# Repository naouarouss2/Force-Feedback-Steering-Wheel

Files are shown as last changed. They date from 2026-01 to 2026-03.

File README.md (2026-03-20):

# DIY FFB Steering Wheel
## What is it ? 🎮
A Force Feedback Wheelbase is a device used in car, truck, bus, or any other 3+ wheeled vehicle (as motorcycles require something different).

The difference between it and a standard game controller is, as the name suggests : **Force Feedback**

Force Feedback is what will create a physical connection between you and the game/simulator you're playing. It will allow you to feel every bump, road imperfection, steering stiffness, vibration... as if you're driving in real life.

## Features ✅
-  **Direct drive**, making it very silent, providing the most accurate and lossless feedback
-  **12-15Nm Force Feedback** (**5.7-7.1x** more powerful than the Logitech G29)
-  **12 Programmable buttons** (Depends on the wheel attached)
-  **Auto center**
-  **0.01125° sensitivity**, making it comparable to some high-end wheelbases on the market

## Why do I want to build it ? 🛠️
I have always wanted to have a simracing setup. Whenever I go to a mall or a gaming café and see a simracing setup, I run like a kid to try it.

I once tried a professional direct drive setup with a motion setup, and this really made me more excited about simracing.

The problem is that the only decent wheelbase available in Tunisia is the Logitech G29 family. They are pretty nice, but overpriced in Tunisia, and it really didn't really fill my heart and satisfy my requirements.

So I wanted to build my own wheelbase, tweaked to my likings and preferences, with endless upgrading and tuning options.

## 3D Design 🎨
I designed everything inside Solidworks, as I am pretty familiar with it, and I already have the CSWA certification.
I divided the design in 2 parts :
-  First, the wheelbase sub-assembly :

| **Full design** | **Aluminium machined parts** | **3D Printed parts** | **Commercial parts** |
|---|---|---|---|
||||

-  Next, the steering wheel sub-assembly

| **Full design** | **Aluminium machined parts** | **3D Printed parts** | **Commercial parts** |
|---|---|---|---|
|||||

And here are pictures of the finished product !


## Wheelbase PCB ⚡
To minimize wiring and make things simpler and cleaner inside, I made a PCB for the wheelbase

| **3D View** | **PCB Routing View** | **Schematics** | 
|---|---|---|
||||

## Wiring Diagrams 🔌
### Wheelbase wiring diagram
fb58e3fb-e4d4-41d1-b4ad-96e4c3caae32
### Steering wheel wiring diagram (made on KiCad, but no PCB)


## Wheelbase Firmware 💡
For the wheelbase, I will be using [OpenFFBoard](https://github.com/Ultrawipf/OpenFFBoard)

## Disclaimer ⚠️

**This project is still under development.**

**Some parts and dimensions in the design should be fixed when I get my hands on the actual componens.**

**Firmware is still untested.**

**This wheelbase can output very high amounts of torque, that may cause injuries.**

**Building is not recommended until everything is made safe ans stable, and the project is completed.**

**If you want to build this project before completion, I would recommend switching from aluminium paddle shifters to 3D Printed ones using the same STEP files, and starting with low force feedback power until the system feels familiar and reassuring, or better, until I finish the development and make sure that the project is safe to use.**

## License 🔓

This project is put opensource. 

Building as is, is allowed.

Remixing is also allowed, as long as the original project is linked and credited.

## Credits ❤️

Project made by **Oussama NAOUAR**

Total logged working time : **~68hrs**

Made as part of the **HackClub Blueprint** program, asking for a grant.

## BOM 💵

This table format below is slightly different from what I originally made in Google Sheets. To to understand it better, I would recommend checking out [BOM.pdf](BOM.pdf)

All prices and shippings costs below are shown in **USD**. For local Tunisian shops, prices and costs were **converted from TND to USD**, based on the exchange rates between **17-12-2025** and **16-12-2025**.

Prices shown below are **non-discounted** prices. These may vary, especially on Aliexpress and other non-local shops.

Shipping costs shown below are **indicative**, based on what Aliexpress and other non-local shops/manufacturers displayed. **These costs may change**.

Articles shown as (x2) are originally only sold as single items, not a 2pcs bundle, with a x2 quantity. And that is done to show the most accurate pricing and shipping fee.

|Type |Component name |Product description |Shop / Manufacturer |Local|URL |Unit price|Shipping|Product Amount|Product Total (excluding shipping)|Product Total (with shipping)|
|---|---|---|---|-----|---|---|---|---|---|---|
|Commercial parts |20*20mm Aluminium Profile|Used to make the wheelbase frame |Seli |Yes  |https://seli.tn/product/20x20-profile-aluminium-industriel-dk/ |15,6 |0 |1 |15,6 |15,6 |
| |40*20mm Aluminium Profile|Used to make the wheelbase frame |Seli |Yes  |https://seli.tn/product/20x40-profile-aluminium-industriel-r6/ |22,5 |0 |1 |22,5 |22,5 |
| |SK16 Brackets |Used to mount the motor in place |Seli |Yes  |https://seli.tn/product/sk16-support-d-arbre-en-aluminium-diam-16/ |3,11 |0 |2 |6,22 |6,22 |
| |UFL004 Bearings |Used to guide the shaft in rotation |Aliexpress |No |https://ar.aliexpress.com/item/1005007098430647.html |17,9 |0 |1 |17,9 |17,9 |
| |ODESC 52V Driver |Used to drive the motor and process FFB Logic |Aliexpress |No |https://ar.aliexpress.com/item/1005005763345874.html |78 |13,2 |1 |78 |91,2 |
| |STM32H743VIT6 Board |Used to control the ODESC board along with the game inputs |Aliexpress |No |https://ar.aliexpress.com/item/1005009563874211.html |11,55 |4,05 |1 |11,55 |15,6 |
| |2000PPR Rotary Encoder |Used to determine the steering wheel's position |Aliexpress |No |https://ar.aliexpress.com/item/1005004387342695.html |15,35 |7,82 |1 |15,35 |23,17 |
| |30-tooth 30mm pulley |Used to tie the encoder's shaft to the steering wheel shaft |Aliexpress |No |https://ar.aliexpress.com/item/1005008678109995.html |4,67 |0 |1 |4,67 |4,67 |
| |Quick release mechanism  |Used to mount the steering wheel to the wheelbase |Aliexpress |No |https://ar.aliexpress.com/item/1005009121231549.html |62,86 |0 |1 |62,86 |62,86 |
| |GX12 Connector kit (M/F) |Used to connect input peripherals to the wheelbase |Tunisian Smart Innovation|Yes  |https://tuni-smart-innovation.com/products/connecteur-male-et-femelle-gx12-4-broches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 |1,49 |0 |5 |7,45 |7,45 |
| |120mm Fan |Used to cool the wheelbase's electronics |2BTrading |Yes  |https://2btrading.tn/ventilateur-radiateur/2391-ventilateur-dc12v-034a-12x12x38cm.html |10,73 | |1 |10,73 |10,73 |
| |XT60M connector |Used to power the wheelbase |Cothings |Yes  |https://cothings.net/products/connecteur-amass-xt60e-m-male |1,73 |0 |1 |1,73 |1,73 |
| |Endstop switch |Game inputs |Cothings |Yes  |https://cothings.net/products/copie-de-capteur-de-temperature-thermistance-ntc-100k-ntc-mf52at-1 |0,45 |0 |2 |0,9 |0,9 |
| |Pushbutton |Game inputs |Cothings |Yes  |https://cothings.net/products/mini-bouton-poussoir-rond-a-reinitialisation-automatique-bleu-etanche-pbs-33b-12mm-2-broches |0,86 |0 |8 |6,88 |6,88 |
| |Hall effect sensor |Used to calibrate the wheel's initial position |Cothings |Yes  |https://cothings.net/products/ky-024-capteur-a-effet-hall-analogique-pour-vitesse-et-comptage |1,55 |0 |1 |1,55 |1,55 |
| |36V 500W Power supply |Used to power the wheelbase |Aliexpress |No |https://ar.aliexpress.com/item/1005003923590693.html |50,53 |10,49 |1 |50,53 |61,02 |
| |GT2-6 400mm belt |Used to connect the shaft pulley to the encoder pulley |2BTrading |Yes  |Courroie GT2-6 400mm |3 |0 |1 |3 |3 |
| |Seed XIAO RP2040 |Microcontroller for the steering wheel |Aliexpress |No |https://ar.aliexpress.com/item/1005003682505451.html |4,78 |4,52 |1 |4,78 |9,3 |
| |Steering Wheel |The actual steering wheel |Aliexpress |No |https://ar.aliexpress.com/item/1005009791304312.html |25,99 |42,53 |1 |25,99 |68,52 |
| |TJA1051 |CAN transceiver |Aliexpress |No |https://ar.aliexpress.com/item/1005005569468051.html |4,1 |0 |1 |4,1 |4,1 |
| |12V Buck Converter |Used to power the fan |Aliexpress |No |https://ar.aliexpress.com/item/1005008597548688.html |2,6 |7,28 |1 |2,6 |12,48 |
| |5V Buck Converter |Used to power the MCU and other peripherals |Aliexpress |No |https://ar.aliexpress.com/item/1005008597548688.html |2,6 | |1 |2,6 | |
| |USB-C Female Connector |Used to connect the wheelbase to the computer |Aliexpress |No |https://ar.aliexpress.com/item/1005009695057393.html |11,62 |0 |1 |11,62 |11,62 |
| |USB-C 90° cable |Used to transfer the USB connection from the PCB to the external connector|Aliexpress |No |https://ar.aliexpress.com/item/1005002708307702.html |6,4 |4,79 |1 |6,4 |11,19 |
| |USB-C Breakout Board | |Aliexpress |No |https://ar.aliexpress.com/item/1005004807492800.html |4,19 |0 |1 |4,19 |4,19 |
| |JST-XH 4 Pin Connector |Used to make cable connections easier |Tunisian Smart Innovation|Yes  |https://tuni-smart-innovation.com/products/connecteur-jst-xh2-54-4-broches-male-femelle-avec-cable-de-20-cm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 |0,7 |0 |5 |3.5 |3.5 |
| |JST-XH 3 Pin Connector |Used to make cable connections easier |Tunisian Smart Innovation|Yes  |https://tuni-smart-innovation.com/products/connecteur-jst-xh2-54-3-broches-male-femelle-avec-cable-de-20-cm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|0,62 |0 |1 |0,62 |0,62 |
| |JST-XH 2 Pin Connector |Used to make cable connections easier |Tunisian Smart Innovation|Yes  |https://tuni-smart-innovation.com/products/connecteur-jst-xh-2-broches-male-femelle-avec-cable-de-20-cm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 |0,49 |0 |1 |0,49 |0,49 |
| |M2X10 Screw |Screw diameter = 2mm, length = 10mm |Already have | |N/A |0 |0 |4 |0 |0 |
| |M3x10 Screw |Screw diameter = 3mm, length = 10mm |Already have | |N/A |0 |0 |8 |0 |0 |
| |M3x16 Screw |Screw diameter = 3mm, length = 16mm |Already have | |N/A |0 |0 |10 |0 |0 |
| |M4x8 Screw |Screw diameter = 4mm, length = 8mm |Already have | |N/A |0 |0 |8 |0 |0 |
| |M4x16 Screw |Screw diameter = 4mm, length = 16mm |Already have | |N/A |0 |0 |4 |0 |0 |
| |M5x16 Screw |Screw diameter = 5mm, length = 16mm |Already have | |N/A |0 |0 |6 |0 |0 |
| |M5x36 Screw |Screw diameter = 5mm, length = 36mm |Already have | |N/A |0 |0 |4 |0 |0 |
| |M5x50 Screw |Screw diameter = 5mm, length = 50mm |Already have | |N/A |0 |0 |6 |0 |0 |
| |M6x20 Screw |Screw diameter = 6mm, length = 20mm |Already have | |N/A |0 |0 |4 |0 |0 |
| |M10x16 Screw |Screw diameter = 10mm, length = 16mm |Already have | |N/A |0 |0 |2 |0 |0 |
| |M3 Nut |Nut diameter = 3mm |Already have | |N/A |0 |0 |4 |0 |0 |
| |M10 Nut |Nut diameter = 10mm |Already have | |N/A |0 |0 |2 |0 |0 |
| |M3 Aluminium Profile Nut |Nut for aluminium profiles, diameter = 3mm |Seli |Yes  |https://seli.tn/product/ecrou-marteau/ |0,1 |0 |4 |0,4 |0,4 |
| |M4 Aluminium Profile Nut |Nut for aluminium profiles, diameter = 4mm |Seli |Yes  |https://seli.tn/product/ecrou-marteau/ |0,1 |0 |8 |0,8 |0,8 |
| |M5 Aluminium Profile Nut |Nut for aluminium profiles, diameter = 5mm |Seli |Yes  |https://seli.tn/product/ecrou-marteau/ |0,1 |0 |4 |0,4 |0,4 |
| |M6 Aluminium Profile Nut |Nut for aluminium profiles, diameter = 6mm |Seli |Yes  |https://seli.tn/product/ecrou-marteau/ |0,1 |0 |4 |0,4 |0,4 |
| |Table clamps (x2) |Used to mount the wheelbase on the table |Aliexpress |No |https://ar.aliexpress.com/item/1005006458478718.html |47,8 |8,28 |1 |47,8 |56,08 |
| |Hoverboard motor |Used to provide force feedback |Facebook Marketplace |Yes  |N/A |19 |0 |1 |19 |19 |
| |TOTAL | | | | | | | |453,11 |556,07 |
|PCB |Wheelbase PCB |Holds the various electronic components without the need for wiring |JLC PCB |No |N/A |2 |21,91 |1 |2 |21,91 |
|Aluminium machined parts|Front plate | |JLC CNC |No |N/A |8,72 |49,48 |1 |8,72 |72,77 |
| |Back plate | |JLC CNC |No |N/A |10,63 | |1 |10,63 | |
| |Paddle (x2) | |JLC CNC |No |N/A |3,94 | |1 |3,94 | |
|GRAND TOTAL | | | | | | | | |478,4 |650,75 |

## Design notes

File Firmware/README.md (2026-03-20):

In this folder, you will find the firmware for the ~wheelbase~, as well as the firmware for the steering wheel itself.

**Disclaimer ⚠️ :** None of these firmwares had been tested on hardware.

For the OpenFFBoard configurator tool, you can find it in this [official OpenFFBoard repository](https://github.com/Ultrawipf/OpenFFBoard-configurator/tree/9eee2b5ffe44f2dec1c6d2eae4a0ad987d53b5c8) :

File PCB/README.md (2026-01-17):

Here you will find all of the Wheelbase PCB files.

Extensions  :
-  Project : .kicad_pro
-  Schematic : .kicad_sch
-  PCB : .kicad_pcb
-  Footprint libraries created and used : .pretty
-  Symbol libraries created and used : .kicad_sym

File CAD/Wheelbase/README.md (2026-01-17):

Hexagonal holes in the 3D Printed parts are for magnets (not modeled).
Aluminium profile nuts were not modeled. But every screw that is going in an aluminium profile rail will need a matching nut.

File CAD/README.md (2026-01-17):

Here you will find all of the design ressources for this project.

**Disclaimer ⚠️ :** Some dimensions may not be accurate yet. Some files will be updates as soon as I get my hands on the actual parts to take measurements.

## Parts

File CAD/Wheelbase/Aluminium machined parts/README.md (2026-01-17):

The back plate should have threaded holes for the electronics mounting holes (M3 screw holes).

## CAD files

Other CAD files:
CAD/Full_assembly.STEP
CAD/Steering Wheel/Steering_wheel_sub-assembly.STEP
CAD/Wheelbase/Wheelbase sub-assembly.STEP
CAD/Steering Wheel/3D Printed parts/Paddle Holder.STEP
CAD/Steering Wheel/Aluminium machined parts/Paddle.STEP
CAD/Steering Wheel/Commercial parts/QR Sample.STEP
CAD/Wheelbase/3D Printed parts/Clamp Surface Flattener.STEP
CAD/Wheelbase/Aluminium machined parts/Front plate.STEP
CAD/Wheelbase/Commercial parts/KFL004.STEP
CAD/Steering Wheel/3D Printed parts/Paddle Shifter Mount.STEP
CAD/Wheelbase/3D Printed parts/Hall Eff Sensor Mount.STEP
CAD/Wheelbase/Aluminium machined parts/Back plate.STEP
CAD/Wheelbase/Commercial parts/Side 2040 profile.STEP
CAD/Wheelbase/PCB.step
CAD/Steering Wheel/3D Printed parts/Back Enclosure.STEP
CAD/Wheelbase/3D Printed parts/Top cover.STEP
CAD/Wheelbase/Commercial parts/Clamp Sample.STEP
CAD/Steering Wheel/3D Printed parts/Front.STEP
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

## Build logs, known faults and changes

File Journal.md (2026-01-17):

<!--
  This journal is auto generated by Hack Club Blueprint.
-->

## 12/17/2025 - 3D Design Pt.1  

_Time spent: 2.5h_  

**17-12-2025**
Today, I started working on the 3D Design of the wheelbase.

To get some inspiration, I went on YouTube and watched a lot of different designs of wheelbases that used a hoverboard for FFB.

The simplest design is to use aluminium profiles for the frame and motor mounting. And to hold the steering wheel axis, I decided to go with 5mm cnc-cut aluminium sheets for the front and back plates. And for cool aesthetics, I will design some 3D-printed parts to complete the enclosure.

For today, I started by designing the 30*30mm aluminium profiles that will go on the sides between the front and back plates.


I then went on to design the front and back plates.

And after that, I designed the aluminium profile that would hold the hoverboard mounting brackets.

And finally, I put everything inside an assembly to start seeing what the wheelbase will look like.


Up until now, except for the aluminium profiles' sketches, every dimension is roughly entered, just to get a better idea of what the design will look like. 
As I get further into the 3D design, and get a better overall idea about the project and components' dimensions, I will enter the right dimensions.

## 12/18/2025 6:29 PM - 3D Design Pt.2  

_Time spent: 2.0h_  

**17-12-2025**
After I took a dinner break, I got back to CAD.

I changed the side aluminium profiles to 20*20mm instead of 30*30mm since they're a bit cheaper, and will make it easier to link them together using the L brackets. I also corrected the 20*40mm profile sketch.

After doing some research, I found that the most popular hoverboard motor size is 6.5 inches. So I went on Grabcad and imported a motor model.

After importing the motor, I designed the SK16 mounting bracket that I'll be using to secure the motor to the aluminium profile.

After doing the assembly, I noticed that the motor will sit a bit lower than the enclosure, so I needed to raise it.

I designed a riser to go between the middle profile and the SK16 brackets, but I didn't want to put a plastic part in the motor holding assembly. So I changed the bottom aluminium profiles to some 20*40mm to raise the motor higher, and therefore eliminate the need for a plastic riser.

I also squared up the front and back plates to make it easier to understand the dimensions.



## 12/18/2025 6:49 PM - 3D Design Pt.3  

_Time spent: 1.0h_  

**18-12-2025**
Today, since I had 2hrs of free time at school, I decided to make some adjustments to my current 3D design.

First of all, I lowered the middle profile, the one to hold the motor on, to sit right between the bottom side profiles. This will make for a much sturdier mount with screws on the sides, instead of relying on friction generated by the nuts and L brackets.

But this made it mandatory to have a 3D Printed riser underneath the SK16 brackets.
I did a lot of experimenting to make the spacer as short as possible, but the minimum height I could go with was 23mm.

I also made the entire wheelbase height a bit smaller, to have the motor sticking out a bit on the upper side and have better aesthetics when designing the 3D Printed enclosure.

I also made the wheelbase much shorter, as I decided to make a 3D-printed enclosure to go on the back to house the electronics.

Up until now, my design is very inspired from this design made by "Orhan Kökbudak" on Grabcad :
https://grabcad.com/library/direct-drive-wheelbase-1

Here is my design up until now  : 

Of course the tire will be removed from the motor. It's just that I didn't find a way to do it on that specific STEP file :)

Now the next challenge is to find a way to mount the steering wheel shaft to the motor.

## 12/19/2025 7 PM - 3D Design Pt.4  

_Time spent: 4.0h_  

**18-12-2025**
This time, I did some adjustments to what I did last time, and modeled 2 new components.

First of all, I had to find a way to mount the shaft onto the hoverboard motor.

I asked my mechanics teacher and he proposed to make a mount on a lathe using a thick tube (I forgot the material's name). 

This part will then have 6 holes to mount it on the motor, and a hole to mount the shaft using a bushing. But the thickest diameter he had was only 50mm, and that is really thin, as we have to make the mounting holes as far appart as we can, to avoid drilling into the bearing inside the motor.

At first, I didn't want to use a 3D Printed part for the most critical component of this project. But then, I decided to make a thick part that will be printed in PETG with 100% Infill, and it should work just fine. I saw people doing the same thing, and they didn't have any problems.

So I hopped on Solidworks and drilled some holes on the motor model, and then designed the shaft mount.
At first, I put some approximate shaft dimensions since I didn't decide the shaft diameter.
I tried making it with the biggest fillet possible to make it as sturdy as it can be.

Then I went on the internet, and chose 16mm as shaft diameter, and asjusted the mount accordingly.


Then, I decided to use a traditional rotary encoder, unlike most people on the internet who used magnetic encoders, since it will reduce complication and eliminate the need to drill through the motor.

The encoder will be linked to the shaft using a belt and pulley setup.

I didn't find any good models online of the encoder, so I designed one myself following a datasheet on Aliexpress.


I then proceeded to make the encoder mount. 
It took me a lot of prototyping. At first I made a model that should be mounted on the top side of the bottom aluminium profiles. But that would make the encoder really close to the shaft.

I didn't decide the pulleys that I'll be using so I wanted to space them apart, and make space for a belt tensioner.

So I made a mount that will stick from the side of the profile.


And finally, I went back on the internet to choose the pulleys. Since it was already very late at night, I left their 3D design for the next time.

Here's what I achieved up to this time. 



## 12/19/2025 10 PM - 3D Design Pt.5  

_Time spent: 3.3h_  

**19-12-2025**
Today, I made a very important step-up in the 3D Design.

**1. Encoder Pulleys**

Yesterday, I chose some pulleys with an 8mm bore diameter. I thought that I'll make a part of the shaft thinner using the lathe, but I didn't think about how I'm gonna slide the shaft pulley in its slot. So I had to look for pulleys with a much bigger bore, and unfortunately, these aren't available in Tunisia. 

At first, I thought about building a pulley in the shaft mount which will be 3D Printed, but I didn't wanna rely on 3D Printing for precision. The whole point of the pulley setup is better resolution; 3D printing might ruin that.

After a lot of research, and trying to understand pulley names, I fould on Aliexpress a pulley with 20mm bore diameter. So I made a sample3D pulley in Solidworks to see how it will be mounted. I also switched to a 20mm shaft, which will be sturdier.
I also made a sample pulley design for the encoder.

Since the shaft pulley turned out to be bigger than expected, I made the wheelbase larger to make space for a pulley tensioner. I also slightly modified the encoder mount to sit slightly higher

**2. External Design**

I completely redesigned the front and back plates.

They are larger now, and feature a nice and dynamic design in my opinion.
I also adjusted the mounting holes positions to make space for the 3D-printed enclosure.
The top aluminium profiles are now mounted at an angle.



## 12/20/2025 8 PM - 3D Design Pt. 6 ; A major redesign !  

_Time spent: 1.5h_  

**20-12-2025**
Last time, I tried to replicate Moza's wheelbase design. But I went by mind, no visual reference, so I got it very wrong !
This time, I took a closer look at Moza's wheelbase design and got onto redesigning the entire face plate.
I also found a new way to mount the encoder without the need to use a belt tensioner, so this enabled me to make the wheelbase less wide. I didn't design the new encoder mount yet, but I started by removing the old one and narrowing the wheelbase.


## 12/20/2025 10 PM - CAD Pt.7 ; Failed pulley system redesign attempt  

_Time spent: 2.0h_  

**20-12-2025**
As I said in my previous journal, I found a better way to mount the encoder, that will eliminate the need for a belt tensioner. I got inspired by this design on YouTube :
https://youtu.be/X-Dd3wjQ4uM?si=eNiLrp9AvPEiq4_C

Basically, the encoder is mounted on the back side of the motor, on the same rails as the motor mounting shafts. And this will allow the encoder to slide left and right to get the right amount of belt tension.
But this required a very big pulley that will be mounted on the back side of the motor rotor, and it had to be custom built.

I first made the new encoder mount that will also be 3D printed just like the older one.

Then I added it to the assembly, and everything was looking pretty nice at this point.


Now came the big motor pulley design. And I first thought that I would find ressources and standard dimensions like most normalized parts out there. But I really couldn't find any.
I tried copying the design mentioned earlier, but I couldn't get the STEP file to something that I can reliably get measurements from.
I tried following this YouTube Tutorial, https://youtu.be/6EBqo_BrOmA?si=bFQslmDhV668M_lL but the teeth came out really big, and I couldn't fit 120 teeth in a diameter smaller than the motor's.

So as of now, I think that I will keep the old design, make the wheelbase larger, and design a belt tensioner later.

## 12/21/2025 - CAD Pt.8 ; Success in making the pulley  

_Time spent: 1.2h_  

**20-12-2025**
The great thing about me is that I don't give up easily.
So after dinner, I kept looking for ways to make the pulley, and I found this tutorial uploaded by Solidworks :
https://youtu.be/rjmKaswKXUc?si=Y-1p3jga44CPzpXg
So I followed it and made my custom 120-tooth pulley that will be mounted on the back of the motor.

Next, I made a sample 30-tooth pulley to be mounted on the encoder to have a 4:1 ratio to have 4x the encoder resolution.

Next, I mounted everything in the assembly, and here's what it looks like now :


## 12/22/2025 1 AM - Cad Pt.9  

_Time spent: 3.0h_  

**21-12-2025**
**1. Front Bearing**
To finish with the front plate, I searched for 20mm bearings and found a model called UFL004.
This bearing has a way to mount it with screws to the front plate, thus without needing to make custom brackets...
So I designed a sample model without details, just the important dimensions

Then, I made holes accordingly in the front plate to house this bearing.
https://youtu.be/vjENDQarwxI?si=C9ZFouVhPo-rN4WJ
**2. Back Plate**
Nothing special here. Saved a copy of the front plate, removed the bearing holes, and added it to the assembly.

**3. The enclosure**
Since I'm now pretty confident that the front and back plate designs won't change, I made the external enclosure.

This enclosure will be printed in 4 separate parts : Left, Right, Upper, Lower enclosure, so I designed each part on its own to fit flush with the plates and aluminium profiles.

I also kept the bottom aluminium rails exposed since they will be used for the desk mount.

Since the front plate's sketch is very complicated, I tried looking for a way to make the part inside the assembly to make it easier. So this time, I sketched the enclosure parts directly inside of the assembly, thanks to this tutorial :
 
It is the first time that I make a part within the assembly in Solidworks. And this will certainly help me a lot in this project and in the future project.



## 12/22/2025 11 PM - CAD Pt.10 ; Electronics Enclosure  

_Time spent: 3.0h_  

**22-12-2025**
This time, I made the enclosure for the electronics, that will be mounted at the back, behind the Aluminium back plate.

I used that amazing feature that allows you to design a part within the assembly, and it made my life a lot easier again :)

I first started by designing a very simple enclosure.

Then, I started thinking about the ports that I'll be using for future pedals, shifter, button box... connections.

At first, I thought about making a PCB with RJ45 ports, but then said that making a PCB just to add 4 connectors is really a loss.

So I started searching for available connectors at my local shops and stumbled upon these amazing GX12 connectors.


They directly mount onto the enclosure, so no need for a PCB, screws, whatsoever. I'll just need to solder wires, that's all.

I also decided to add a 120mm fan on the back to cool down the motor driver, and the motor too; that's why I chose a big fan.

And finally, I also decided to put an XT60 connector on the back to power everything on, as the power supply will be separate, so that the wheelbase doesn't get bulkier.



## 12/23/2025 - CAD Pt.10 ; Some vents + components placement  

_Time spent: 2.0h_  

**23-12-2025**
I started by adding some vents on the sides, on both the front and back side panels.



Then, since I chose from the beginning, by watching similar setups online, to use ODESC as a control board for FFB, I downloaded this model from Grabcad to place it in the assembly and start making holes to mount each component. (By the way I'll go through the electronics soon, I just need to finish CAD first).

https://grabcad.com/library/odesc-v4-2-bldc-motor-driver-controller-1

The guy did a really good job at making a very detailed model. But unfortunately, my computer only has 8GB of ram, and an iGPU. So here is where the struggle begins :)

Immediately after adding the component to the assmebly to verify dimensions etc... everything started going very very slow on my computer. So from now on, everything I did later was really slow, including some modifications to the back panel to make mounting holes, and making the back enclosure a bit shorter.

But eventually, I placed it along with the included resistor. And I placed them on the far right to make them close to the power supply connector, and to take benefit of a maximum airflow coming from the vents to the fan.
Here is how it is mounted : 


## 12/24/2025 2 AM - CAD Pt.11 ; Steering Wheel Hub  

_Time spent: 3.5h_  

**23-12-2025**
Today, I decided to take a break from the wheelbase design, and start working on the wheel itself.
For a first wheel, I decided to make things pretty simple and reliable.

I decided to use a Momo steering wheel or similar, like the ones used in drift cars. I still didn't choose the model, but they all have the same 6-screw mounting system.
The wheel will also feature a quick release system. 

I spent a lot of time on Aliexpress looking for a reliable and easy to mount quick release system. 
A lot of them tricked me since they showed cheap prices at first, but they were all "Welcome deals".
The cheapest decent one that I found is this one.
https://ar.aliexpress.com/item/1005009121231549.html
And bonus : Someone already used it for a simracing setup in the reviews !

With that in mind, I went to design a shaft mount for this quick release module. 


Next, I went on to design the hub that will be stuck to the steering wheel. This hub will contain all of the buttons, paddle shifters... and all of the wiring.
First, I designed the back plate that will be mounted to the QR mechanism.

There are 12 holes : 6 for the QR mechanism, and 6 to mount the front plate and the steering wheel.

Here is the front plate, that will house (for now, just as an alpha prototype version) 8 buttons.

The 2 plates will be spaced by about 3.5cm to make space for the wiring inside + paddle shifters mounted on the sides.
The 2 plates will be spaced by using screw spacers.

And to hide everything, I made this enclosure


Then, I made a small cylinder with approx dimensions as a sample for the quick release mechanism, just to tell that it's there.

And finally, I made everything into a sub-assembly :


## 12/24/2025 7 PM - CAD Pt.12  

_Time spent: 2.5h_  

**24-12-2025**
I know, CAD is taking very long, but we're very close :)

First of all, I modified all of the wheel hub parts so that they become modular and linked to eachother, so that when I edit one of them, I don't get errors, and every part get automatically rebuilt.
I did that by sketching the parts inside of the assembly.

Then, I added two joystick holes to the front plate
.

After that, I got to designing the magnetic paddle shifter assemblies.
I tried to do something very similar to what this guy did :
https://youtu.be/Fp4gQ_euMsg?si=-S9PfVIbnG-W44iQ
I started by making the paddle

Then I slowly made the other parts by myself, keeping in mind that guy's amazing work.
After that, I put everything into a new sub assembly.

Up until now, I thought that everything had been done properly. But that changed quickly when I tried putting the sub-assembly into the wheel hub sub-assembly.



Not only was the assembly designed backwards, meaning that to activate the switch you need to push the paddle, but the mounting holes were also wrongly placed in a way that they would hide behind the quick release mechanism.

It was very frustrating to see 2hrs of work lost. But it happens !

I think that I'll use the parts from the YouTube video, as fixing my model will take a lot of time.
He provided STL parts in the Google Drive linked in the description, as well as DXF files for the laser-cut parts, from which I will tzke dimensions to put on my design for the mounting holes.

## 12/25/2025 - PCB Design Pt.1 ; First steps in KiCad :)  

_Time spent: 4.5h_  

**25-12-2025**
This time, I decided to take a break from the 3D Design !

Remember when I said that a PCB isn't necessary because I only needed to wire 4 connectors ? Well it turned out that I was wrong.

After doing some more research on YouTube and the OpenFFBoard GitHub and Discord server, it turned that it is a bit more than just connectors.

For the electronics, I will be using  the ODESC board as mentioned before. But on top of that, I will be using :

- An STM32H7 board to handle the game inputs
- A 12V regulator to power on the fan
- A 5V regulator to power the STM32 board along with providing power to the GX12 connectors
- A TJA1051 CAN transcoder so that the ODESC and STM32 board can communicate
- A hall effect sensor 

So to keep things tidy and more reliable (as I always tend to make a mess when wiring up a lot of components manually), I decided to make a small PCB.

Before thinking about the wiring diagram, since I knew the components that I'll be using, I first chose my PCB editor : Altium Designer.

Why Altium ? Because it was the only software that had a STM32H7 board library available online.
And this is a very critical decision so that I don't have bad surprises when I make good progress later on.

At first, I thought that it would be pretty easy to get started, but then I found the software to be very complex, and not beginner friendly.

I started looking for alternatives that supported Altium libraries, and I found KiCad, so I downloaded it eventually. And believe me, the light theme and simple-looking interface really comforted my mind and brought me my motivation back.

To test it, I tried by importing the Altium Library. The import process was pretty easy, but I soon ran into issues. 

The board was imported in 2 symbols, and the biggest and most important one isn't working at all. I couldn't place any wire. And when going to PCB editor, it automatically inserted two whole boards instead of one, and none of them was working.

And since I already apreciate the user-friendly interface, I decided to make my own symbol and footprint for the STM32H7 board.

I found this tutorial on YouTube, and slowly but surely, I started getting the hang of it.

https://youtu.be/OzF5vsgkLAY?si=zL08rsIuo40u2LD9
https://youtu.be/NiSkKemLK_8?si=Aa3ntH2me7qxCW7M

I followed the tutorial while following an image of the board online. I chose a generic board since I thought that they were the cheapest, and made the symbol accordingly. But when I checked on Aliexpress, these generic boards were cheap indeed, but shipping to Tunisia was very expensive. So I chose to make the WeAct board instead, since it was cheaper overall. So I saved it and kept it. Maybe I'll need it in the future, who knows !?

And fortunately, the corrupt library had the exact same symbol pin layout as the WeAct one, so it made it easier since I basically had to copy it. Here's what I made :


Next, is the footprint layout !

I downloaded the 3D STEP model from this Github

https://github.com/WeActStudio/MiniSTM32H7xx

And by taking measurements from the model in Solidworks, and following the tutorial above, here is what I came up with :


To connect components to this PCB, I chose to use some JST XH connectors. Essentially 2-pin, 4-pin and 5-pin variants.

I found the footprints in KiCad, but I could not find the symbols. So I made a symbol for each variant and linked it to its matching footprint.



## 12/26/2025 - PCB Design Pt.2 ; The schematics  

_Time spent: 3.5h_  

**26-12-2025**
First, I made the missing components for the pcb, the symbol + footprint.
The missing components were :

- 3P JST XH connector for the Hall Effect Sensor
- TJA1051 CAN Transceiver
- The buck converters (I will use 2 of the same model for both 5V and 12V outputs)

Next, after continuing to watch the tutorial series that I linked yesterday, I started looking for the cheapest PCB manufacturer that makes high quality PCB. And I chose JLC PCB as it was the cheapest of all, and had very good reviews and apparently a good build quality.
Then, by using the link provided in the video's description, I imported all  of the settings and tolerences for JLCPCB machines to KiCad.

After that was done, I started making the schematics for the wheelbase's PCB.
First of all, I placed all of the components in a way that would make it more understandable for me to work on. 

For the JST XH connectors, I used : 

- 4 4-Pin connectors for the GX connectors on the wheelbase to connect the peripherals
- A 5-pin connector for the encoder
- A 3-pin connector for the hall effect sensor
- A 2-pin connector for the ODESC CAN input
- A 2-pin connector to power up the electronics from the main 36V power input
- A 2-pin connector to power up the fan from the 12V buck converter
- A 4-pin connector for the ST-Link programmer

I then renamed all of the components so that they make sense.

Then I connected all of the connectors 1st and 2nd pins to GND and +5V respectively, of the 5V buck converter's output.

Then, I wired up the TJA1051 module to a CAN port of the STM32H7 board by following the official datasheet.

Then I wired up all of the 4-pin connectors to different UART ports of the STM32 board, as these will be used to connect peripherals.

And finally, I connected the encoder to 3 timer pins of the STM32H7 board with a 510-Ohm resistor for each channel. I saw people doing that when using a 5V encoder with an STM32 board on VNM discord server, so I thought that it was to protect the 3.3V pins, so I added the resistors.

Here is how the schematics turned out :


## 12/27/2025 2 AM - CAD Pt. 13 ; Wheel Hub Redesign  

_Time spent: 2.0h_  

**27-12-2025**
Back to CAD again :)
At 12:30AM, I got the very bright decision to completely redesign the steering wheel hub !

I started doing some research regarding CNC cutting aluminium sheets, and it is pretty expensive, and useless to be honest.
So I decided to make the steering wheel hub entirely 3D-Printed. 
And this time, I got inspired by Fanatec's Clubsport Universal Hub design.


So first of all, I started designing the face plate, with, just like Fanatec's hub, 4 triangles to hold 3 push buttons each. I made it triangular so that it fits well with the wheel, and kept a big hole for the quick release mechanism to go through, to the wheel itself.


Then I put it inside of an assembly, along with the buttons and the QR sample model to see how everything looks.

After that, I started designing the enclosure that will go behind that plate, and will house the wiring and paddle shifters, directly inside of the assembly.

Unfortunately, the thick enclusure walls meant that most of the quick release mechanism was going to be inside of that enclosure, and make it impossible to operate the mechanism. So I headed back to the front plate design, and made a built-in spacer that would push the quick release mechanism out of the enclosure, just enough so that it can be operated.



For now, I put an approximate spacer thickness since I don't know how thick the quick assembly mechanism really is, and how thick the enclosure will be. So once I finish the hub design, and get my hands on the mechanism, I would be able to insert the right dimensions.

## 12/27/2025 11 PM - PCB Design Pt.3 ; PCB Routing Complete !  

_Time spent: 4.0h_  

**27-12-2025**
This time, I went to finish with the PCB so that I could finish CAD once and for all.

Last time, I made the schematics, so today, all I had to do was the PCB layout and wiring.

I first placed the components as shown in the image below. I wanted the PCB to be as small as possible, and as easy to route as possible.


As you can see, to minimize routing complication, I put the ST-Link connector just above the SDIO header of the STM32 board, the power connector just besides the buck converters' inputs, the encoder resistors just above the header pins...

And since the STM32 board is going to sit on top of headers, I put the resistors under it to minimize space.


At this point in routing, I remembered that JLC PCB prices PCBs smaller than 100x100mm in size at $2. And when I measured the PCB, I found it bigger than 100x100mm, and that's excluding mounting holes.

So I did the layout again, and had to redo most of the routing.

At this point, I finished routing everything but the GND and 5V nets, as I planned to make copper fills for those. 

I also added a 100x100mm cutout outline, and placed M3 mounting holes on each corner to mount it at the back of the wheelbase.

For the copper fills, I first started by making a GND plane at the back side, and that went flawlessly.
 
However, when I tried to make a 5V plane at the front side, I didn't find the option for that.

After asking ChatGPT, I apparently had to connect the 5V net to a power symbol in the schematics. So I did just that. 

And finally, I made my copper fills. 

Here is what the PCB will look like (just suppose that the STM32 board and PCB will be black :) ) :


## 12/28/2025 1 AM - CAD Pt.14 ; Installing the PCB   

_Time spent: 1.0h_  

**28-12-2025**
Since it is almost 1AM, I didn't want to do a big step.

First of all, I modified the wheelbase's back plate to mount the PCB, according to the mounting holes I put earlier in my PCB Design.
Then I added some vents to help cool the motor and the ODESC board since it has a heatsink on the back.


Here is what the electronic's bay will look like :



After that, I got working on the back cover to add a space to mount a female USB-C connector.
From what I understood from the official WeAct STM32H7 schematics, the onboard USB-C connector only uses 2 data pins.

And that will enable me to use this type of female USB-C connectors, as it is very easy to mount.

https://ar.aliexpress.com/item/1005009695057393.html

And to connect the STM32 USB connector to the external one, I will be using a 90° short cable with a breakout board. 

A 90° connector will be used since the PCB design made the STM32 board's connector very close to the JST connector next to it. And unfortunately that is the only layout option I see, that could keep the PCB's size smaller than 100*100mm.

So with that in mind, I followed the dimensions that the seller put in the listing, and made a mounting hole in the back cover. 



## 12/28/2025 8 PM - CAD Pt.15 ; Working on the wheel hub  

_Time spent: 2.5h_  

**28-12-2025**
For testing purposes, I downloaded a 300mm steering wheel from Github to see how the hub will fit.
Even though I will be using a 330mm wheel, I downloaded a 300mm model to get some good margin for the fingers.
Here's how it turned out :

Pretty messed up, right ?
To fix it, I went through a lot of prototyping.
I moved the steering axis to the top to free up space for a microcontroller board below it.

I also had to sacrifice a button on each side on the bottom because I didn't have enough space.

And to get the buttons and their plates positioned right, all I did was testing and evaluating by eye.

And even after the modifications, the buttons were still very close to the wheel, not leaving a comfortable room for the fingers. So I had to make another spacer on the front of the front panel of the hub.

Here is how it turned out in the assembly

After getting the layout about right, I added some side wings on the front plate to mount the paddle shifters that I will design later.


With that done, I got on working on a new paddle shifter design. I didn't really want to use a pre-made design like I said before. I want the project to be 100% my creation.
I got inspired by this design :
https://youtu.be/rf8PqbjdBoI?si=zRmNwDc7QN1vpco3
I started working on the mount that will house magnets on both sides.


As you can see, I made a circular-shaped hole with a hole on each side for an axis, to have a swing arm between the magnets.


I stopped here for lunch unfortunately. I'll finish the design in the afternoon.

## 12/28/2025 9 PM - CAD Pt.16 ; Design complete ! (Well... almost)  

_Time spent: 2.0h_  

**28-12-2025**
After a long break, I got back to work.
First of all, I modified the paddle's design I made before, to fit with the new design

I then got back the paddle holder (swing arm) to add place for the magnets.

Then I put everything into an assembly to see how it looks, and where I will place the endstop switch.

I later decided that I will put the switch on the back side of the assembly so that I will be more free for the dimensions and have more space for wiring.

And to do just that, I will need to make a small extension to the swing arm to avoid the magnet, and to benefit from the space between the top faces of the swing arm and the mount.

And to place the enstop switch, I made a rectangular hole with space for mounting screws.

As you can see, I made everything symetrical since on the left side, everything will be flipped.

Making a design for each side will increase the work, and may increase the cost too, since with my design, I removed more material from the mount than I added on the swing arm.

After that, I put the sub-assebly in the steering wheel's sub assembly, and added the endstop switch on each side.

After doing that, The paddle shifters stood out wider than the wheel itself (even when I drew a 330mm one). So I narrowed down the wheel hub.

I also closed the wheel hub on the back, and added a GX12 connector to connect it to the base.

Here is how the steering wheel sub-assembly turned out.


And finally, I inserted this sub-assembly to the big wheelbase assembly.


Now, all what's left is to make the table mount.

I really can't tell you how happy I got when I saw the whole design coming together !

## 12/29/2025 - CAD Pt.17 ; Small fixes  

_Time spent: 0.5h_  

**29-12-2025**
After taking a closer look at the assembly, I realized that it is pretty far from being complete.
I am still missing :

- The table mount
- Mounting options for the side panels
- Hall effect sensor + magnet mounts
- Holes in the back panel for wires to go through to the controllers

And since it is very very early in the morning (or very late at night), I went with the 2nd option since it was pretty easy and won't take much time.

At first, when I first made the panels, I thought about mounting them with screws and nuts.

But I think that I got a better idea. What if I made some guides to go through the aluminium profiles' rails, and then the panels will be sandwiched between the front and back plates.

So that's what I exactly did. I sketched the guides directly in the assembly, and made 4 20mm guides for each rail using the linear pattern feature to make things quick.



## 12/30/2025 - CAD Pt. 18 ; Fixing mistakes  

_Time spent: 1.5h_  

**29-12-2025**
After making the guides for the side panels yesterday and shutting off my pc, I kept thinking about the project in bed before sleeping. And I realized that what I did was possible in the design, but impossible to make IRL.

You see, to mount the back enclosure, you need to screw it from the inside of the wheelbase, behind the back panel.

And to do that, you need to have the panels removed to access the screws. So if I kept that design, then it would be impossible to either mount the back cover, or the side panels.

So I had o think about other solutions.
I didn't want to add screws on the outside as it will make the wheelbase uglier.

I thought about only modifying the top plate to have screws, and modify the back enclosure and panel to move screws to the top, but that will leave the back enclosure unsecured on the bottom.

I also wanted to make a sliding mechanism, where you mount the side panels like before, and then the back plate, then you put the endlosure slightly below its final position, and slide it upwards, to next secure it with screws on the top.

But that would really complicate things and it would require things to go below the PCB...
So I kept the sliding mechanism on the top and bottom panels, and modified the side panels to be mounted with screws.




This design will make it easier to access the parts on the front (motor, encoder, hall effect sensors...), and will alsomake access for the back cover very easy.

Good thing that it was only a small mistake to be corrected, so it didn't take much time since the previous design only took me 0.5h. But each day, I am more convinced that working with an enormous sleep debt is far from being right. It is not the first mistake I made because of it.

So if there is one piece of advice I could give, is sleep well. Taking a nap and delay work will give much better results than working with a lack of sleep. Even if time is pressing, working while feeling rested will be much quicker and more reliable.

Anyways, since I was pretty tired at this point, I decided to make the simplest thing left, which is a hole in the back panels to go through.


That's it for today. 

Good thing that the deadline was extended, but I will try to get finished with CAD tomorrow.
Already 18 CAD journal entries and I still haven't finished yet.
The only things left are the hall effect sensor mount, and the table mount.

## 1/9/2026 - CAD Pt. 19 ; Hall Effect Sensor Mount  

_Time spent: 1.5h_  

**08-01-2026**
Deadline extension really made me very lazy to work.

Anyways, the last thing but one to do is to design the hall effect sensor mount.

At first, to remove design complications and the need for screws and nuts... I wanted to make a hall effect sensor mount that sticks up from the bottom cover.

I wanted to use the simple sensor on its own. No breakout board or anything.

I wanted to make a clamp style holder. Put a horizontal mount near the shaft mount, put the hall effect sensor on top of it and clamp it using another 3D Printed part and 2 screws.

When I got to this point, I realized that it is a rather dumb idea.

You see, the mount is very fragile. It is very long, which makes it really prone to breaking. And it it does, I'll have to print the entire bottom cover again, which is really a waste of money + making the entire project more difficult to maintain.

Instead, what I want to do, is make a mount that will be screwed on the left lower aluminium profile. And instead of using a simple sensor, I decided to use one with a breakout board, meaning an entire module similar to this one :

A module will enable me to fine tune the sensitivity of the sensor directly within the board itself. This is necessary since the sensitivity needs to be adjusted depending on the magnet's size, strength, distance between the magnet and the sensor... while testing.

Here is the mount I came up with :

Dimensions need to be corrected when I get my hands on the module, since I couldn't find that information online.

Here's how the hall effect sensor module will be mounted :


## 1/11/2026 - CAD Pt. 20 ; Not the last part :/  

_Time spent: 3.5h_  

**10-01-2026**
I really hoped to finish CAD today, but unfortunately, it didn't happen :/
This time, I added all of the screws (I really hope) needed to hold the wheelbase together. 
And this took much longer than expected, so I couldn't really finish the screews needed in the steering wheel sub assembly.

I started by measuring the holes group by group, and measuring the clearance for each screw. Then I proceeded by making the screws (A model, without threads, rounded corners...) by referring to this table :

And finally, I placed all of the 50 screws in their designed places.

This step is very crucial as it will allow me to better understand my design. Not only that, but it also prepares it for the submission.

## 1/12/2026 - CAD Pt. 21 ; FINALLY !  

_Time spent: 4.0h_  

**11-01-2026**
Yes, FINALLY !
This time, the 3D design is finished.


First, I found a way to attach the wheelbase to a table.

I will use these clamps I found on Aliexpress that can be screwed to the wheelbase on those bottom aluminium profiles.

I went on and made a sample part in Solidworks, added the screws, and since the screws will be sticking ou from the clamp, and may dent the table, I designed a 3D printed surface flattener to hide the screws.


Then I went to the steering wheel sub assembly and made and added the necessary screws. 
I also added the screws needed for the quick release mechanism on the wheelbase side, and added a place for the hall effect sensor magnet on the shaft mount.

After all of that was done, and the design was finished, I went ahead and started preparing the design files for the Github repo.

I made a repo, and a local folder, within which I made sub folders for the different project parts.

I then started by placing the files I downloaded from Grabcad, and saved all of the parts I designed in the STEP format and placed them in my directory.  

## 1/15/2026 - Wiring Diagrams  

_Time spent: 1.0h_  

**15-01-2025**
Today, I made the wiring diagrams.
I downloaded some pictures of the multiple components used, and launched Freeform to make the diagrams.
First, I started by the wheelbase's diagram. It will show how components external to the PCB are connected.
fb58e3fb-e4d4-41d1-b4ad-96e4c3caae32
I simplified this diagram when it comes to the encoders and GX12 connectors' connections, so that it doesn't look overwhelming. But here is how they will be connected :

For the GX12 connectors, they will be connected to a male JST-XH connector each, like shown below :
1b0f98cb-818f-4924-b728-17cdcdf095d6
Same thing for the rotary encoder :
d99b77bc-1ca4-4a75-8ace-f9d6f093a1af
For the motor's encoder connector, I will have to check it when I buy it, since they usually differ from a model to another. So I might have to attach a new connector to the motor's encoder if the original one doesn't fit into the ODESC connector.

Now, time for the wheel's wiring diagram. 

The steering wheel will also use a dedicate microcontroller, so that only 4 wires in total (2 signal wires + 2 power wires) go to the wheelbase, and this will also allow for modularity.

I decided to use a Seed XIAO RP2040 microcontroller since I won't need a lot of pins. I also chose it because it runs on 3.3V, so I won't have use a voltage divider so that I don't damage the wheelbase's MCU. It is also compact and will easily fit inside the wheel hub.

It will receive 5V from the wheelbase via the VBUS pin, so that voltage loss/instability won't really bother it.

I made this schematic on KiCad so that it looks more understandable, but I won't make a PCB for it.



## 1/16/2026 - Porting The Code Pt.1 ; Failed attempt  

_Time spent: 3.5h_  

**15-01-2026**
Now that everything is finished, it was time to take care of the firmware.
I will use OpenFFBoard firmware available here :

https://github.com/Ultrawipf/OpenFFBoard/tree/master

It is an opensource firmware that is designed to handle the ODESC board.

The problem is that this firmware is now only compatible with 3 STM32F4 microcontroller models. 

I used the STM32H743VIT6 in my wheelbase, so I have to port the code.

When I did my first research on Bing, the first thing that popped up is this YouTube video :

https://youtu.be/tURj2me-wxE?si=_crX2SMm3uQs-1Zu

At first, this seems like a very good tutorial, as it is apparently a stream replay, so no cuts whatsoever.

I started following the guide bit by bit, but soon started running into some issues.

Apparently STM32CubeIDE changed a lot in 4 years :/ 

The STM32 drivers package wasn't downloaded automatically, so I had to manually download it. 

Also STM32CubeIDE didn't arrange the files like it did on the tutorial.

The tutorial seemed very based on the project he was working on, so he didn't really explain what should be done in general.

I tried fixing the files arrangement and everything, but I then found out that STM32CubeIDE didn't make a .ioc file.

I am very new to STM32Cube ecosystem, as I used to code in ArduinoIDE, so I made Bing and Google research along the tutorial. And apparently to configure FreeRTOS, I needed a .ioc file.

I tried outsmarting STM32CubeIDE :

- Made a blank .ioc file in the project directory, STM32CubeMX didn't recognize it :(
- Copied the original .ioc file from Github for the STM32F407VG board, and tried modifying all of the MCU ID, Model... in notepad. I thought that it will keep the same pin config... When I opened it, STM32CubeMX correctly showed the STM32H7 MCU that I was using, but also showed some errors, and purple pins that apparently meant that something is very wrong. Also some errors on the clock config popped up. Turns out these microcontrollers have very different architectures inside.



Since not everything was porperly kept/reset, and I did it the very hard and direct way, and it showed some errors when I first tried compiling the code, I decided to give up on this tutorial.

I tried looking for other solutions, till I found this one on the ST website.

https://community.st.com/t5/stm32-mcus/how-to-switch-from-one-stm32-to-another-using-stm32cubemx/ta-p/49884

I tried reproducing the same steps mentioned there.

The first attempt resulted in the process taking very long.

I stopped it, and restarted it again, same result.

I thought maybe because it is not the same STM32 family, so I tried with another F4 MCU, and it worked quickly.

I then tried disabling the CAN1 in the original project, since before trying to import it, it shows something related to CAN1.

I also restarted a new importation of the original firmware in parallel.

I tried leaving them work in the background and went on to work on the BOM (not logged into this journal time).

The original firmware finished importing, but showed some error messages.

The firmware without CAN1 still didn't finish. 

I pressed OK on the project that finished importing, and STM32CubeMX again went to a new infinite loading time cycle.

I noticed that when I bring it back to the front of the desktop, fans ramp up, so I kept it there and went to prepare myself for bed.

When I opened task manager, I found it saying efficiency mode.

So what I did, was close the copy of the firmware without CAN1, and in the task manager, I set that process priority to realtime. 

The system felt really sluggish afterwards, but it didn't matter.

I left it there until I finish my doomscrolling session.

And when I heard the PC fans get quieter, I jumped out of bed to save the project, and shut down the PC and sleep.

We'll see how everything goes afterwads.

I know, this entry is very long, but I tried logging my troubleshooting steps...
Note that only hand-on time working on the firmware is logged. BOM, doomscrolling, preparing for sleep isn't counted here :)  

## 1/18/2026 12:03 AM - Porting The Code Pt.2 ; Success  

_Time spent: 1.5h_  

**16-01-2026**
As soon as I got back home from school, I opened my computer, aiming to finally finish the project design to be able to submitt soon.

I opened STM32CubeIDE, and loaded the project that had "finished importing".

When I clicked on Generate Code, some errors popped up.

Slowly but surely, I tried fixing some by myself, while I got some help online for others.

The most important ones I think, are I2C and Timer configurations.

As I am very new to the STM32Cube environment, I struggled a bit, but then I finally was able to generate code.

But in contrast to what I inistially thought, Generate Code only imported the librairies initalized before when I imported the project, along with the pin, buses, and clock configurations.

But already getting all of the librairies and configuration included almost automatically is really nice.
And STM32CubeMX directed me to CubeIDE, so as I thought, a .ioc configuration file was really necessary.

Then I went to the original OpenFFBoard project directory, and tried manually importing and arranging files and folders.

After some time, I tried building the project, I got a bunch of red lines and errors in the console. But upon further inspection it turned out that STM32CubeIDE built all of the open projects at that time, so the errors were related to the first porting attempt I made before.
I closed that project, and tried building again, and SUCCESS !
The code compiled without errors !


After that was done, I proceeded to make the code for the Seed XIAO RP2040 board in Arduino IDE.

I made it in a way that it would only send the button data when a button changes state, so that it doesn't keep sending data and avoid inducing game input lag on the wheelbase's side.

That's it ! The final steps in making the project design is done !

CAD ✅
PCB ✅
Firmware ✅

All that was left to do is preparing the files needed in the Github repo.

And by the time of writing this journal entry, everything was done and added to the repo. Just missing some readme.md files in the sub directories.

PS : Time logged in this journal entry is only the time spent on the codes.

## 1/18/2026 12:40 AM - To sum up (+ banner picture)  

_Time spent: 0.3h_  

**18-01-2026**



I really enjoyed working on this project.

It is a project that I have always dreamed of designing, and hopefully building after I get a grant.

The Blueprint program really motivated me to design this project, and convert my thoughts and ideas to files, and hopefully in the future, a real working system.

Along this 68-hour jouney, I was able to learn a lot of thins, among which was PCB design.

For this project, I designed my first ever PCB on KiCad, and got the occasion to learn how to make symbols and footprints.

This project also sharpened my skills in CAD, and made me use some features I never thought existed. And the thing I was most excited about, was to directly make and edit a new part inside of an assembly.

This project was also my entry gate to the STM32Cube environment. This really clarified the differences between STM32CubeIDE and STM32CubeMX, taught me a bit about MCU configuration...

And most importantly, working on this project late at night, really made me realize the importance of well resting and a good sleep schedule.

My PC, despite the pretty low specs, did a great job. It really struggled in the 3D design when it started coming up together, but I tried learning how to optimize ressources usage... I tried to model everything part of the design, and that would affect the design, but had to exclude some components that wouldn't affect the design.

I am really grateful and happy for what I was able to make and achieve. Making this project in less than a month, most of it (arount 55hrs) before the previous submission deadline was really challenging, especially considering that I was working on a HackPad, another project (the Amplifier model), and studying in parallel.

This really shows that when you put your mind and time into something, you are really beyond able to achieve it.

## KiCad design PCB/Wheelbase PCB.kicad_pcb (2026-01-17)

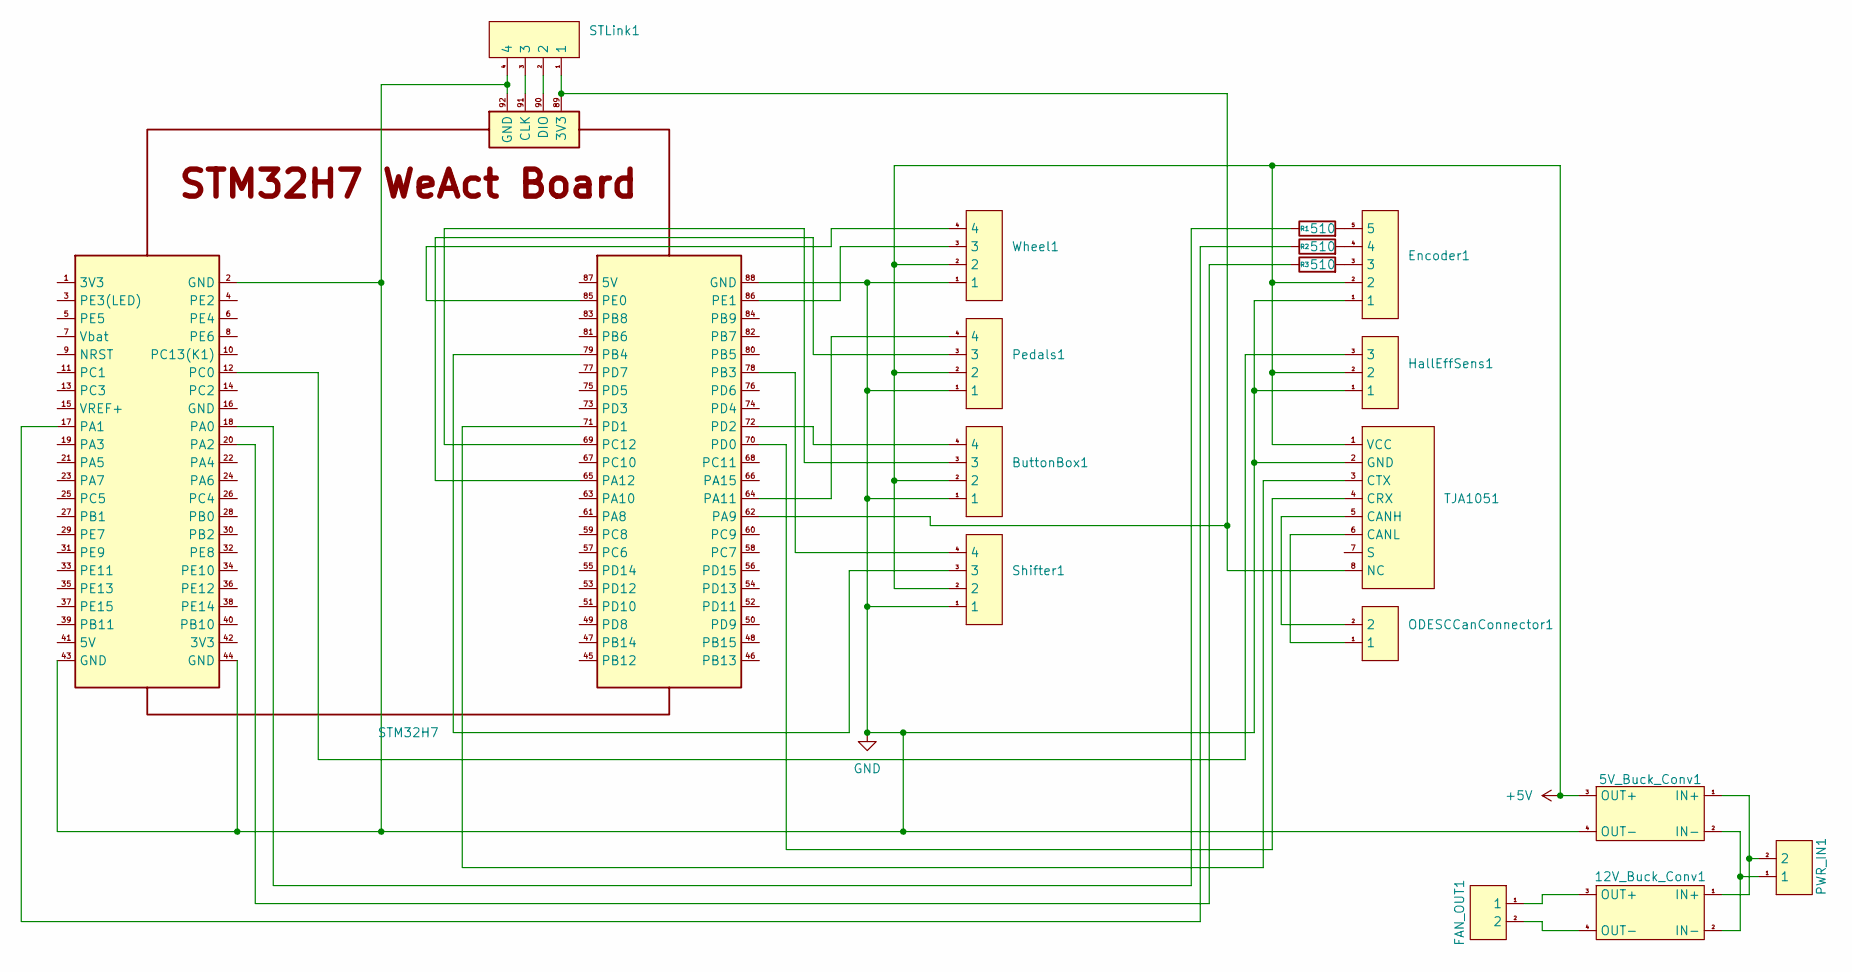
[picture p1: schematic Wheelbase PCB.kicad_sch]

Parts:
5V_Buck_Conv1, 12V_Buck_Conv1: Buck Converter
ButtonBox1: JST_XH_B4B-XH-A_1x04_P2.50mm_Vertical
Encoder1: JST_XH_B5B-XH-A_1x05_P2.50mm_Vertical
FAN_OUT1: JST_XH_B2B-XH-A_1x02_P2.50mm_Vertical
HallEffSens1: JST_XH_B3B-XH-A_1x03_P2.50mm_Vertical
ODESCCanConnector1: JST_XH_B2B-XH-A_1x02_P2.50mm_Vertical
PWR_IN1: JST_XH_B2B-XH-A_1x02_P2.50mm_Vertical
Pedals1: JST_XH_B4B-XH-A_1x04_P2.50mm_Vertical
R1, R2, R3: 510; R_Axial_DIN0207_L6.3mm_D2.5mm_P10.16mm_Horizontal
STLink1: JST_XH_B4B-XH-A_1x04_P2.50mm_Vertical
STM32H7: WeAct Board
Shifter1: JST_XH_B4B-XH-A_1x04_P2.50mm_Vertical
TJA1051: TJA1051 Board
Wheel1: JST_XH_B4B-XH-A_1x04_P2.50mm_Vertical

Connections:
+5V: 5V_Buck_Conv1.3 (OUT+), ButtonBox1.2, Encoder1.2, HallEffSens1.2, Pedals1.2, Shifter1.2, TJA1051.1 (VCC), Wheel1.2
GND: 5V_Buck_Conv1.4 (OUT-), ButtonBox1.1, Encoder1.1, HallEffSens1.1, Pedals1.1, STLink1.4, STM32H7.2 (GND), STM32H7.43 (GND), STM32H7.44 (GND), STM32H7.88 (GND), STM32H7.92 (GND), Shifter1.1, TJA1051.2 (GND), Wheel1.1
unnamed: 5V_Buck_Conv1.1 (IN+), 12V_Buck_Conv1.1 (IN+), PWR_IN1.2
unnamed: 5V_Buck_Conv1.2 (IN-), 12V_Buck_Conv1.2 (IN-), PWR_IN1.1
unnamed: 12V_Buck_Conv1.3 (OUT+), FAN_OUT1.1
unnamed: 12V_Buck_Conv1.4 (OUT-), FAN_OUT1.2
unnamed: Encoder1.3, R3.2
unnamed: Encoder1.4, R2.2
unnamed: Encoder1.5, R1.2
unnamed: STLink1.3, STM32H7.91 (CLK)
unnamed: STLink1.2, STM32H7.90 (DIO)
unnamed: R1.1, STM32H7.18 (PA0)
unnamed: R2.1, STM32H7.17 (PA1)
unnamed: R3.1, STM32H7.20 (PA2)
unnamed: STLink1.1, STM32H7.62 (PA9), STM32H7.89 (3V3), TJA1051.8 (NC)
unnamed: Pedals1.4, STM32H7.64 (PA11)
unnamed: Pedals1.3, STM32H7.65 (PA12)
unnamed: STM32H7.78 (PB3), Shifter1.4
unnamed: STM32H7.79 (PB4), Shifter1.3
unnamed: HallEffSens1.3, STM32H7.12 (PC0)
unnamed: ButtonBox1.3, STM32H7.69 (PC12)
unnamed: STM32H7.70 (PD0), TJA1051.4 (CRX)
unnamed: STM32H7.71 (PD1), TJA1051.3 (CTX)
unnamed: ButtonBox1.4, STM32H7.72 (PD2)
unnamed: STM32H7.85 (PE0), Wheel1.4
unnamed: STM32H7.86 (PE1), Wheel1.3
unnamed: ODESCCanConnector1.2, TJA1051.5 (CANH)
unnamed: ODESCCanConnector1.1, TJA1051.6 (CANL)

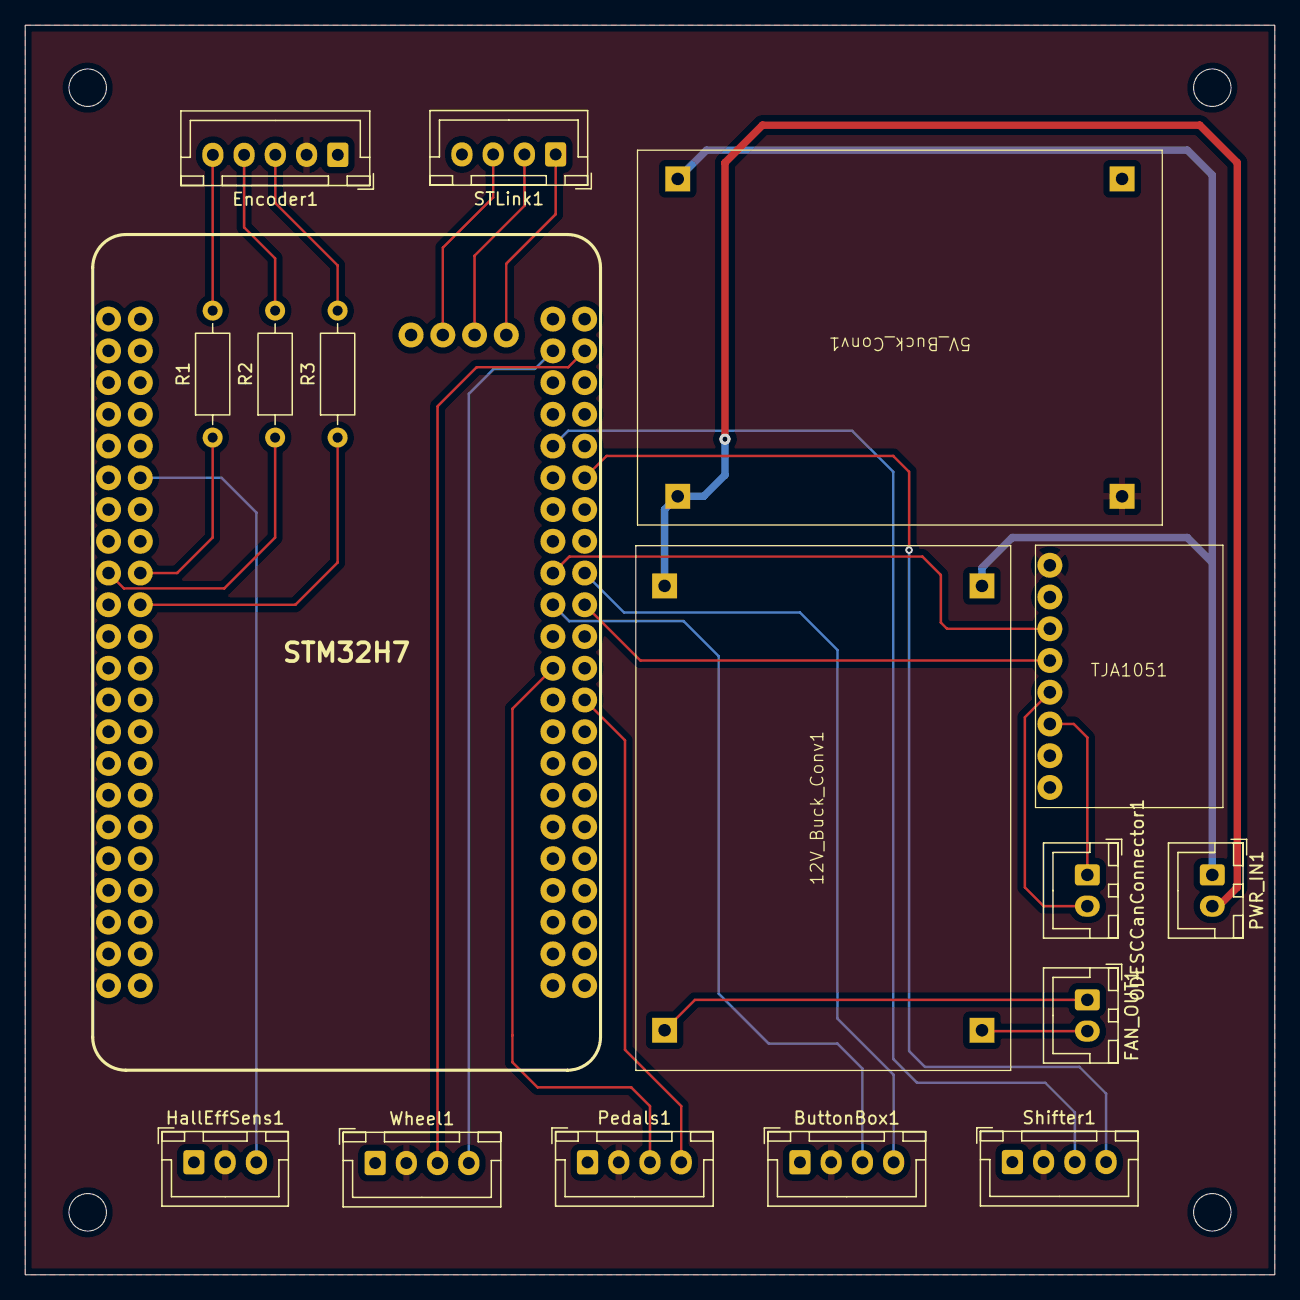
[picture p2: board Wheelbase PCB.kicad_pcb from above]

Board: 4 copper layers, 100.0 x 100.0 mm, 17 parts (0 on the bottom side), 28 nets.

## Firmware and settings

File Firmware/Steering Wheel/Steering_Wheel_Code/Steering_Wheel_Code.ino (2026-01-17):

const uint8_t rowPins[] = {3, 4, 2};
const uint8_t colPins[] = {26, 27, 28, 29};

const uint8_t NUM_ROWS = sizeof(rowPins);
const uint8_t NUM_COLS = sizeof(colPins);

bool lastState[NUM_ROWS][NUM_COLS];

void setup() {
  for (uint8_t r = 0; r < NUM_ROWS; r++) {
    pinMode(rowPins[r], INPUT_PULLUP);
  }

  for (uint8_t c = 0; c < NUM_COLS; c++) {
    pinMode(colPins[c], OUTPUT);
    digitalWrite(colPins[c], HIGH);
  }

  Serial1.begin(115200);
  memset(lastState, 0, sizeof(lastState));
}

void loop() {
  for (uint8_t c = 0; c < NUM_COLS; c++) {
    digitalWrite(colPins[c], LOW);
    delayMicroseconds(5);

    for (uint8_t r = 0; r < NUM_ROWS; r++) {
      bool pressed = (digitalRead(rowPins[r]) == LOW);

      if (pressed != lastState[r][c]) {
        lastState[r][c] = pressed;

        Serial1.print(c);
        Serial1.print(",");
        Serial1.print(r);
        Serial1.print(",");
        Serial1.println(pressed ? 1 : 0);
      }
    }

    digitalWrite(colPins[c], HIGH);
  }
}

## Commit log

2026-01-17 Add README
    [120mm_fan_asm.stp, 30T Pulley.STEP, 50W 2Ohm Power Resistor.step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]
2026-03-20 Add Wheelbase Firmware section to README
    Added section for Wheelbase Firmware using OpenFFBoard.
